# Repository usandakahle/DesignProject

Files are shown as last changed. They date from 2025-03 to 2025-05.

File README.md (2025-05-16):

# Micromouse Power Module System

This project is the power module circuit for the EEE3088F design project that provides power to the micromouse system

## Features

-  Boost Converter (3.7V → 5V @ 1.5A)
-  LDO Regulator (5V → 3.3V @ 300mA)
-  Dual H-Bridge Motor Driver (DRV8833 for 4x brushed DC motors)
-  High-Side Load Switches (TPS2HB50-Q1, 2 channels @ 1A each)
-  Physical ON/OFF switch with <30µA shutdown current
-  USB-C Female Connector
-  CH224K PD Negotiation (9V)
-  Linear Voltage Regulator, LM7805 (5V)
-  LiPo Battery Charging IC, TC4056A
-  Small PCB footprint, JLCPCB-ready
-  -All features and components are sourced from JLCPCB (https://jlcpcb.com/parts/all-electronic-components) 
  
---

##  Design Overview

- Input: 3.7V Li-ion (1S1P)
- USB-C Input: 9V
- Voltage Regulation:
  - Boost: MT3608
  - 3.3V Regulator: AMS1117-3.3 or TLV75533P
  - 5V Regulator: LM7805
- Motor Driver: DRV8833, controls 4 DC motors bidirectionally
- Load Switches:TPS2HB50-Q1 with configurable ILIM resistors
- ON/OFF Circuit: Slide switch + pMOS + NPN low-quiescent design

---

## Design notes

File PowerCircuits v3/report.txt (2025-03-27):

Error: Update symbols CN1 CN1 from 'batt_conn:B2B-PH-K-S(LF)(SN)' to 'batt_conn:B2B-PH-K-S(LF)(SN)': *** symbol not found ***
Error: Update symbols LED1 LED1 from 'led101:KT-0603R' to 'led101:KT-0603R': *** symbol not found ***
Error: Update symbols U6 U12 from 'npn:2N2222A' to 'npn:2N2222A': *** symbol not found ***
Error: Update symbols U5 U11 from 'tc4056:TC4056A' to 'tc4056:TC4056A': *** symbol not found ***
Update symbol TP4 from 'Connector:TestPoint' to 'Connector:TestPoint': OK
Update symbol TP3 from 'Connector:TestPoint' to 'Connector:TestPoint': OK
Update symbol TP5 from 'Connector:TestPoint' to 'Connector:TestPoint': OK
Update symbol TP7 from 'Connector:TestPoint' to 'Connector:TestPoint': OK
Update symbol TP6 from 'Connector:TestPoint' to 'Connector:TestPoint': OK
Update symbol C2 from 'Device:C_Small' to 'Device:C_Small': OK
Update symbol R6 from 'Device:R_Small_US' to 'Device:R_Small_US': OK
Update symbol R7 from 'Device:R_Small_US' to 'Device:R_Small_US': OK
Update symbol C10 from 'Device:C_Small' to 'Device:C_Small': OK
Update symbol C9 from 'Device:C_Small' to 'Device:C_Small': OK
Update symbol #PWR08 from 'power:GND' to 'power:GND': OK
Update symbol C1 from 'Device:C_Small' to 'Device:C_Small': OK
Update symbol U5 from 'Power_Management:TPS22929D' to 'Power_Management:TPS22929D': OK
Update symbol C3 from 'Device:C_Small' to 'Device:C_Small': OK
Update symbol C7 from 'Device:C_Small' to 'Device:C_Small': OK
Update symbol #PWR09 from 'power:GND' to 'power:GND': OK
Update symbols J1 J1 from 'Connector_Generic:Conn_02x16_Odd_Even' to 'Connector_Generic:Conn_02x16_Odd_Even': OK
Update symbol U3 from 'Regulator_Linear:AP2112K-3.3' to 'Regulator_Linear:AP2112K-3.3': OK
Update symbol U2 from 'Regulator_Switching:MT3608' to 'Regulator_Switching:MT3608': OK
Update symbol C5 from 'Device:C_Small' to 'Device:C_Small': OK
Update symbol C12 from 'Device:C_Small' to 'Device:C_Small': OK
Update symbol R4 from 'Device:R_Small_US' to 'Device:R_Small_US': OK
Update symbol R3 from 'Device:R_Small_US' to 'Device:R_Small_US': OK
Update symbol #PWR014 from 'power:GND' to 'power:GND': OK
Update symbol #PWR015 from 'power:GND' to 'power:GND': OK
Update symbol #PWR013 from 'power:GND' to 'power:GND': OK
Update symbol U6 from 'Driver_Motor:DRV8833PWP' to 'Driver_Motor:DRV8833PWP': OK
Update symbol C11 from 'Device:C_Small' to 'Device:C_Small': OK
Update symbol U4 from 'Power_Management:TPS22929D' to 'Power_Management:TPS22929D': OK
Update symbol C4 from 'Device:C_Small' to 'Device:C_Small': OK
Update symbol R1 from 'Device:R_Small_US' to 'Device:R_Small_US': OK
Update symbol R2 from 'Device:R_Small_US' to 'Device:R_Small_US': OK
Update symbol C6 from 'Device:C_Small' to 'Device:C_Small': OK
Update symbol #PWR010 from 'power:GND' to 'power:GND': OK
Update symbol Q1 from 'Transistor_FET:AO3401A' to 'Transistor_FET:AO3401A': OK
Update symbol #PWR07 from 'power:GND' to 'power:GND': OK
Update symbol #PWR017 from 'power:GND' to 'power:GND': OK
Update symbol #PWR06 from 'power:GND' to 'power:GND': OK
Update symbol #PWR05 from 'power:GND' to 'power:GND': OK
Update symbol #PWR018 from 'power:GND' to 'power:GND': OK
Update symbol #PWR023 from 'power:GND' to 'power:GND': OK
Update symbol D1 from 'Device:D_Schottky' to 'Device:D_Schottky': OK
Update symbol #PWR021 from 'power:GND' to 'power:GND': OK
Update symbol #PWR01 from 'power:GND' to 'power:GND': OK
Update symbol R5 from 'Device:R_Small_US' to 'Device:R_Small_US': OK
Update symbol U1 from 'Driver_Motor:DRV8833PWP' to 'Driver_Motor:DRV8833PWP': OK
Update symbol U7 from 'Slide Switch Korean Hroparts Elec:K3-1391B-51' to 'Slide Switch Korean Hroparts Elec:K3-1391B-51': OK
Update symbol #PWR024 from 'power:GND' to 'power:GND': OK
Update symbol #PWR016 from 'power:GND' to 'power:GND': OK
Update symbol #PWR02 from 'power:GND' to 'power:GND': OK
Update symbol C8 from 'Device:C_Small' to 'Device:C_Small': OK
Update symbol #PWR03 from 'power:GND' to 'power:GND': OK
Update symbol #PWR04 from 'power:GND' to 'power:GND': OK
Update symbol #PWR019 from 'power:GND' to 'power:GND': OK
Update symbols R6 R12 from 'Device:R_Small_US' to 'Device:R_Small_US': OK
Update symbols C1 C14 from 'Device:C_Small' to 'Device:C_Small': OK
Update symbols R5 R14 from 'Device:R_Small_US' to 'Device:R_Small_US': OK
Update symbols TP2 TP2 from 'Connector:TestPoint' to 'Connector:TestPoint': OK
Update symbols JP2 JP2 from 'Jumper:Jumper_2_Open' to 'Jumper:Jumper_2_Open': OK
Update symbols R2 R8 from 'Device:R_Small_US' to 'Device:R_Small_US': OK
Update symbols R1 R10 from 'Device:R_Small_US' to 'Device:R_Small_US': OK
Update symbols C2 C15 from 'Device:C_Small' to 'Device:C_Small': OK
Update symbols C3 C13 from 'Device:C_Small' to 'Device:C_Small': OK
Update symbols R10 R13 from 'Device:R_Small_US' to 'Device:R_Small_US': OK
Update symbols R4 R11 from 'Device:R_Small_US' to 'Device:R_Small_US': OK
Update symbols TP1 TP1 from 'Connector:TestPoint' to 'Connector:TestPoint': OK
Update symbols JP1 JP1 from 'Jumper:Jumper_2_Open' to 'Jumper:Jumper_2_Open': OK
Update symbols U2 U10 from 'Regulator_Linear:LM7805_TO220' to 'Regulator_Linear:LM7805_TO220': OK
Update symbols R3 R9 from 'Device:R_Small_US' to 'Device:R_Small_US': OK
Update symbol U8 from 'FUC-24F11-SNLB1:FUC-24F11-SNLB1' to 'FUC-24F11-SNLB1:FUC-24F11-SNLB1': OK
Update symbol U13 from 'INA219AIDCNR:INA219AIDCNR' to 'INA219AIDCNR:INA219AIDCNR': OK
Update symbol U9 from 'CH224K:CH224K' to 'CH224K:CH224K': OK

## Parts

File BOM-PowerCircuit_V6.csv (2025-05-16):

Comment | Designator | Footprint | LCSC | Quantity
1k | R10,R11,R14 | R_0402_1005Metric_Pad0.72x0.64mm_HandSolder | C11702 | 3
2.2 uF | C4,C8 | C_0402_1005Metric_Pad0.74x0.62mm_HandSolder | C12530 | 2
AO3401A | Q1 | SOT-23 | C15127 | 1
10nF | C6 | C_0402_1005Metric_Pad0.74x0.62mm_HandSolder | C15195 | 1
10nF | C11,C12,C14,C15,C5 | C_0402_1005Metric_Pad0.74x0.62mm_HandSolder | C15525 | 5
6.8k | R8 | R_0805_2012Metric_Pad1.20x1.40mm_HandSolder | C17772 | 1
1 | R4,R5,R6,R7 | R_1206_3216Metric_Pad1.30x1.75mm_HandSolder | C17928 | 4
KT-0603R | LED1 | LED0603-RD | C2286 | 1
75k | R1 | R_0603_1608Metric_Pad0.98x0.95mm_HandSolder | C23242 | 1
D_Schottky | D1 | D_SMA | C2480 | 1
10k | R2,R9 | R_0402_1005Metric_Pad0.72x0.64mm_HandSolder | C25744 | 2
47k | R3 | R_0402_1005Metric_Pad0.72x0.64mm_HandSolder | C25792 | 1
2k | R12 | R_0402_1005Metric_Pad0.72x0.64mm_HandSolder | C4109 | 1
TPS22929D | U4,U5 | SOT-23-6 | C415177 | 2
5.6k | R13 | R_0805_2012Metric_Pad1.20x1.40mm_HandSolder | C4382 | 1
DRV8833PWP | U1,U12 | TSSOP-16_L5.0-W4.4-P0.65-LS6.4-BL-EP | C50506 | 2
LM7805S/TR | U10 | TO-263-3_L8.6-W10.2-P2.54-LS14.4-BR | C507146 | 1
AP2112K-3.3 | U3 | SOT-23-5 | C51118 | 1
1uF | C1,C10,C13,C2,C3,C7,C9 | C_0402_1005Metric_Pad0.74x0.62mm_HandSolder | C52923 | 7
FUC-24F11-SNLB1 | U8 | USB-C-SMD_C67380 | C67380 | 1
TC4056A | U11 | ESOP-8_L4.9-W3.9-P1.27-LS6.0-BR-EP3.3 | C84051 | 1
MT3608 | U2 | SOT-23-6 | C84817 | 1
MMBT2222A_C8512 | U14 | SOT-23-3_L2.9-W1.3-P1.90-LS2.4-BR | C8512 | 1
INA219AIDCNR | U13 | SOT-23-8_L3.0-W1.7-P0.65-LS2.8-BR | C87469 | 1
K3-1391B-51 | U7 | SW-TH_K3-1391B-51 | C92656 | 1
CH224K | U9 | ESSOP-10_L4.9-W3.9-P1.0-LS6.0-TL-EP | C970725 | 1
External Load out | TP6 | TestPoint_Pad_1.0x1.0mm |  | 1
TestPoint | TP3 | TestPoint_Pad_1.0x1.0mm |  | 1
Jumper_2_Open | JP3 | SolderJumper-2_P1.3mm_Open_TrianglePad1.0x1.5mm |  | 1
TestPoint | TP2 | TestPoint_Pad_1.0x1.0mm |  | 1
3.3V out | TP5 | TestPoint_Pad_1.0x1.0mm |  | 1
Jumper_2_Open | JP1 | SolderJumper-2_P1.3mm_Open_TrianglePad1.0x1.5mm |  | 1
5V out | TP4 | TestPoint_Pad_1.0x1.0mm |  | 1
Jumper_2_Open | JP4 | SolderJumper-2_P1.3mm_Open_TrianglePad1.0x1.5mm |  | 1
Jumper_2_Open | JP2 | SolderJumper-2_P1.3mm_Open_TrianglePad1.0x1.5mm |  | 1
Ext load out | TP7 | TestPoint_Pad_1.0x1.0mm |  | 1
TestPoint | TP1 | TestPoint_Pad_1.0x1.0mm |  | 1

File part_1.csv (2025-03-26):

Source: | C:\Users\Bronwyn Biggs\OneDrive - University of Cape Town\UCT\THIRD Year\EEE3088F Design Principles\MM Project\part_1\part_1.kicad_sch
Date: | 2025/03/24 22:11:09
Tool: | Eeschema 7.0.1
Generator: | C:\Program Files\KiCad\7.0\bin\scripting\plugins/bom_csv_grouped_by_value_with_fp.py
Component Count: | 2
Ref | Qnty | Value | Cmp name | Footprint | Description | Vendor | DNP
J1 | 1 | Conn_02x16_Odd_Even | Conn_02x16_Odd_Even | Connector_PinHeader_2.54mm:PinHeader_2x16_P2.54mm_Vertical | Generic connector, double row, 02x16, odd/even pin numbering scheme (row 1 odd numbers, row 2 even numbers), script generated (kicad-library-utils/schlib/autogen/connector/)
U1 | 1 | INA219AxD | INA219AxD | Package_SO:SOIC-8_3.9x4.9mm_P1.27mm | Zero-Drift, Bidirectional Current/Power Monitor (0-26V) With I2C Interface, SOIC-8

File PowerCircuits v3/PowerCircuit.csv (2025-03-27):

Source: | C:\Users\Sandakahle\OneDrive - University of Cape Town\3rd Year\EEE3088F\Project\CAD\PowerCircuits\PowerCircuit.kicad_sch
Date: | 2025/03/27 11:51:07
Tool: | Eeschema 7.0.1
Generator: | C:\Program Files\KiCad\7.0\bin\scripting\plugins/bom_csv_grouped_by_value.py
Component Count: | 56
Collated Components:
Item | Qty | Reference(s) | Value | LibPart | Footprint | Datasheet | DNP | LCSC | Part #
1 | 5 | C1, C3, C7, C9, C10 | 1uF | Device:C_Small | Capacitor_SMD:C_1206_3216Metric_Pad1.33x1.80mm_HandSolder | ~ |  |  | C1848
2 | 1 | C2 | 1 uF | Device:C_Small | Capacitor_SMD:C_1206_3216Metric_Pad1.33x1.80mm_HandSolder | ~
3 | 2 | C4, C11 | 2.2 uF | Device:C_Small | Capacitor_SMD:C_0402_1005Metric_Pad0.74x0.62mm_HandSolder | ~ |  |  | C12530
4 | 2 | C5, C12 | 10 uF | Device:C_Small | Capacitor_SMD:C_1206_3216Metric_Pad1.33x1.80mm_HandSolder | ~
5 | 2 | C6, C8 | 0.01uF | Device:C_Small | Capacitor_SMD:C_0402_1005Metric_Pad0.74x0.62mm_HandSolder | ~ |  |  | C1524
6 | 1 | C13 | 1uF | Device:C_Small | Capacitor_SMD:C_0402_1005Metric_Pad0.74x0.62mm_HandSolder | ~
7 | 2 | C14, C15 | 10uf | Device:C_Small | Capacitor_SMD:C_0402_1005Metric_Pad0.74x0.62mm_HandSolder | ~
8 | 1 | CN1 | B2B-PH-K-S(LF)(SN) | batt_conn:B2B-PH-K-S(LF)(SN) | batt_conn:CONN-TH_B2B-PH-K-S | https://item.szlcsc.com/142630.html |  | C131337
9 | 1 | D1 | D_Schottky | Device:D_Schottky | Diode_SMD:D_SMA | ~ |  |  | C2480
10 | 1 | J1 | Conn_02x16_Odd_Even | Connector_Generic:Conn_02x16_Odd_Even | Connector_PinHeader_2.54mm:PinHeader_2x16_P2.54mm_Vertical | ~
11 | 2 | JP1, JP2 | Jumper_2_Open | Jumper:Jumper_2_Open | Jumper:SolderJumper-2_P1.3mm_Open_TrianglePad1.0x1.5mm | ~
12 | 1 | LED1 | KT-0603R | led101:KT-0603R | led101:LED0603-RD | https://item.szlcsc.com/347874.html |  | C2286
13 | 1 | Q1 | AO3401A | Transistor_FET:AO3401A | Package_TO_SOT_SMD:SOT-23 | http://www.aosmd.com/pdfs/datasheet/AO3401A.pdf
14 | 1 | R1 | 75k | Device:R_Small_US | Resistor_SMD:R_0603_1608Metric_Pad0.98x0.95mm_HandSolder | ~ |  |  | C23242
15 | 1 | R2 | 10k | Device:R_Small_US | Resistor_SMD:R_0805_2012Metric_Pad1.20x1.40mm_HandSolder | ~ |  |  | C17414
16 | 1 | R3 | 47k | Device:R_Small_US | Resistor_SMD:R_0805_2012Metric_Pad1.20x1.40mm_HandSolder | ~ |  |  | C17713
17 | 2 | R4, R5 | 1 | Device:R_Small_US | Resistor_SMD:R_0603_1608Metric_Pad0.98x0.95mm_HandSolder | ~ |  |  | C22936
18 | 2 | R6, R7 | 0.4 | Device:R_Small_US | Resistor_SMD:R_0603_1608Metric_Pad0.98x0.95mm_HandSolder | ~
19 | 1 | R8 | 6.8k | Device:R_Small_US | Resistor_SMD:R_0402_1005Metric_Pad0.72x0.64mm_HandSolder | ~
20 | 1 | R9 | 10k | Device:R_Small_US | Resistor_SMD:R_0402_1005Metric_Pad0.72x0.64mm_HandSolder | ~
21 | 3 | R10, R11, R14 | 1k | Device:R_Small_US | Resistor_SMD:R_0402_1005Metric_Pad0.72x0.64mm_HandSolder | ~
22 | 1 | R12 | 2k | Device:R_Small_US | Resistor_SMD:R_0402_1005Metric_Pad0.72x0.64mm_HandSolder | ~
23 | 1 | R13 | 6k | Device:R_Small_US | Resistor_SMD:R_0402_1005Metric_Pad0.72x0.64mm_HandSolder | ~
24 | 3 | TP1, TP2, TP3 | TestPoint | Connector:TestPoint | TestPoint:TestPoint_Pad_1.0x1.0mm | ~
25 | 1 | TP4 | 5V out | Connector:TestPoint | TestPoint:TestPoint_Pad_1.0x1.0mm | ~
26 | 1 | TP5 | 3.3V out | Connector:TestPoint | TestPoint:TestPoint_Pad_1.0x1.0mm | ~
27 | 1 | TP6 | External Load out | Connector:TestPoint | TestPoint:TestPoint_Pad_1.0x1.0mm | ~
28 | 1 | TP7 | Ext load out | Connector:TestPoint | TestPoint:TestPoint_Pad_1.0x1.0mm | ~
29 | 2 | U1, U6 | DRV8833PWP | Driver_Motor:DRV8833PWP | Package_SO:HTSSOP-16-1EP_4.4x5mm_P0.65mm_EP3.4x5mm_Mask2.46x2.31mm_ThermalVias | http://www.ti.com/lit/ds/symlink/drv8833.pdf
30 | 1 | U2 | MT3608 | Regulator_Switching:MT3608 | Package_TO_SOT_SMD:SOT-23-6 | https://www.olimex.com/Products/Breadboarding/BB-PWR-3608/resources/MT3608.pdf
31 | 1 | U3 | AP2112K-3.3 | Regulator_Linear:AP2112K-3.3 | Package_TO_SOT_SMD:SOT-23-5 | https://www.diodes.com/assets/Datasheets/AP2112.pdf
32 | 2 | U4, U5 | TPS22929D | Power_Management:TPS22929D | Package_TO_SOT_SMD:SOT-23-6 | http://www.ti.com/lit/ds/symlink/tps22929d.pdf
33 | 1 | U7 | K3-1391B-51 | Slide Switch Korean Hroparts Elec:K3-1391B-51 | footprint:SW-TH_K3-1391B-51 | https://item.szlcsc.com/93849.html?ref=editor&logined=true |  | C92656
34 | 1 | U8 | FUC-24F11-SNLB1 | FUC-24F11-SNLB1:FUC-24F11-SNLB1 | footprint:USB-C-SMD_C67380 | https://item.szlcsc.com/68475.html |  | C67380
35 | 1 | U9 | CH224K | CH224K:CH224K | footprint:ESSOP-10_L4.9-W3.9-P1.0-LS6.0-TL-EP | https://item.szlcsc.com/2976729.html |  | C970725
36 | 1 | U10 | LM7805_TO220 | Regulator_Linear:LM7805_TO220 | Package_TO_SOT_THT:TO-220-3_Vertical | https://www.onsemi.cn/PowerSolutions/document/MC7800-D.PDF
37 | 1 | U11 | TC4056A | tc4056:TC4056A | tc4056:ESSOP-10_L4.9-W3.9-P1.0-LS6.0-TL-EP | https://atta.szlcsc.com/upload/public/pdf/source/20220909/99A730BF861B4E3F85141583932B02D1.pdf |  | C84051
38 | 1 | U12 | 2N2222A | npn:2N2222A | npn:TO-92-3_L4.8-W3.7-P2.54-R | https://item.szlcsc.com/308449.html |  | C358533
39 | 1 | U13 | INA219AIDCNR | INA219AIDCNR:INA219AIDCNR | footprint:SOT-23-8_L3.0-W1.7-P0.65-LS2.8-BR | https://item.szlcsc.com/155588.html |  | C87469

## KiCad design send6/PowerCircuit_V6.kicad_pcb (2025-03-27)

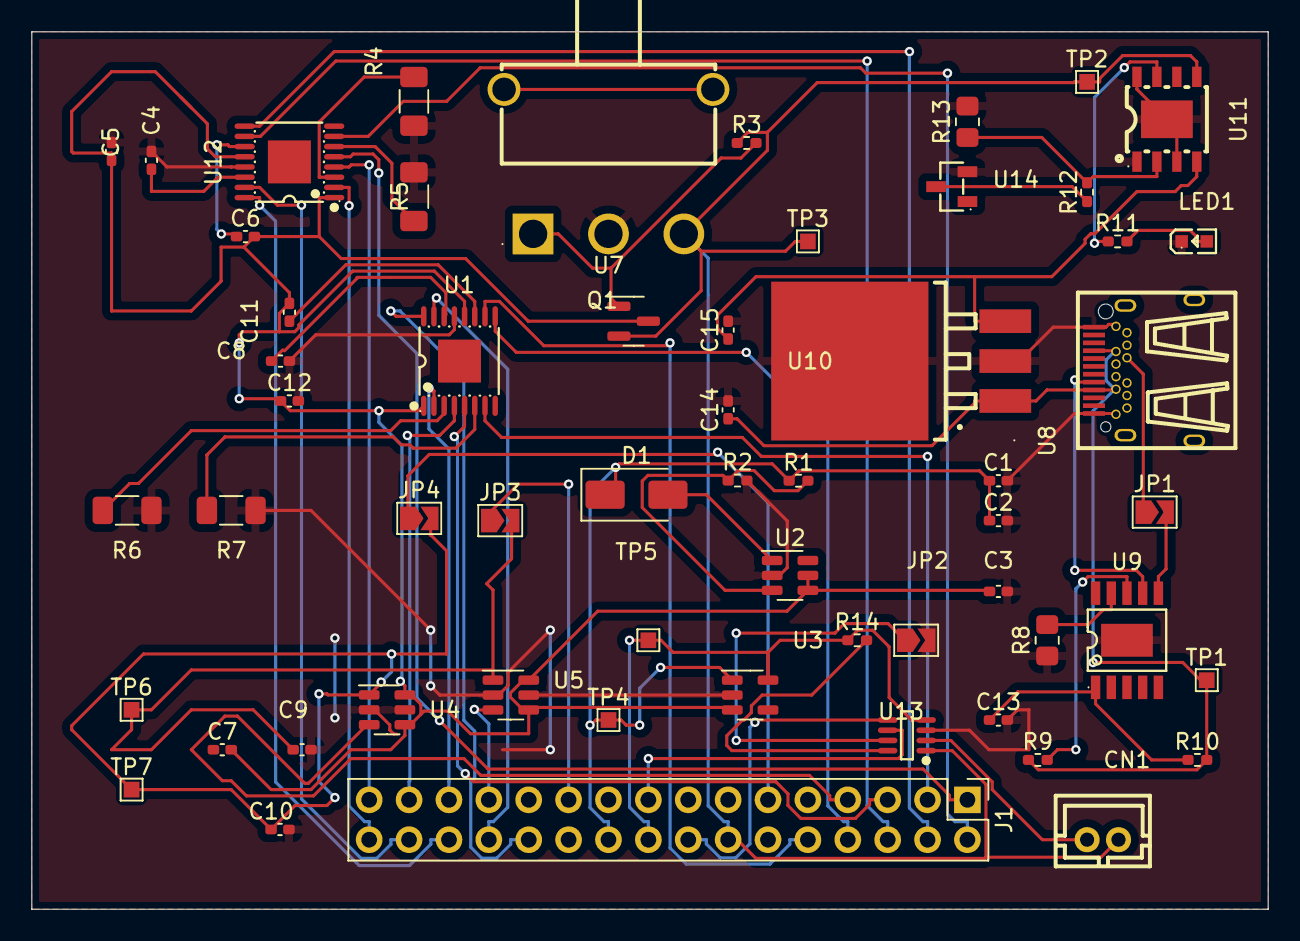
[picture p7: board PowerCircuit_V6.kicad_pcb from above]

Board: 2 copper layers, 78.7 x 55.9 mm, 58 parts (0 on the bottom side), 55 nets.

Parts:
C1, C2, C3, C7, C9, C10, C13: 1uF; C_0402_1005Metric_Pad0.74x0.62mm_HandSolder
C4, C8: 2.2 uF; C_0402_1005Metric_Pad0.74x0.62mm_HandSolder
C5, C12: 10 uF; C_0402_1005Metric_Pad0.74x0.62mm_HandSolder
C6, C11: 10nF; C_0402_1005Metric_Pad0.74x0.62mm_HandSolder
C14, C15: 10uF; C_0402_1005Metric_Pad0.74x0.62mm_HandSolder
CN1: B2B-PH-K-S(LF)(SN); CONN-TH_B2B-PH-K-S
D1: D_Schottky; D_SMA
J1: Conn_02x16_Odd_Even; PinHeader_2x16_P2.54mm_Vertical
JP1, JP2, JP3, JP4: Jumper_2_Open; SolderJumper-2_P1.3mm_Open_TrianglePad1.0x1.5mm
LED1: KT-0603R; LED0603-RD
Q1: AO3401A; SOT-23
R1: 75k; R_0402_1005Metric_Pad0.72x0.64mm_HandSolder
R2, R9: 10k; R_0402_1005Metric_Pad0.72x0.64mm_HandSolder
R3: 47k; R_0402_1005Metric_Pad0.72x0.64mm_HandSolder
R4, R5, R6, R7: 1; R_1206_3216Metric_Pad1.30x1.75mm_HandSolder
R8: 6.8k; R_0805_2012Metric_Pad1.20x1.40mm_HandSolder
R10, R11, R14: 1k; R_0402_1005Metric_Pad0.72x0.64mm_HandSolder
R12: 2k; R_0402_1005Metric_Pad0.72x0.64mm_HandSolder
R13: 5.6k; R_0805_2012Metric_Pad1.20x1.40mm_HandSolder
TP1, TP2, TP3: TestPoint; TestPoint_Pad_1.0x1.0mm
TP4: 5V out; TestPoint_Pad_1.0x1.0mm
TP5: 3.3V out; TestPoint_Pad_1.0x1.0mm
TP6: External Load out; TestPoint_Pad_1.0x1.0mm
TP7: Ext load out; TestPoint_Pad_1.0x1.0mm
U1, U12: DRV8833PWP; TSSOP-16_L5.0-W4.4-P0.65-LS6.4-BL-EP
U2: MT3608; SOT-23-6
U3: AP2112K-3.3; SOT-23-5
U4, U5: TPS22929D; SOT-23-6
U7: K3-1391B-51; SW-TH_K3-1391B-51
U8: FUC-24F11-SNLB1; USB-C-SMD_C67380
U9: CH224K; ESSOP-10_L4.9-W3.9-P1.0-LS6.0-TL-EP
U10: LM7805S/TR; TO-263-3_L8.6-W10.2-P2.54-LS14.4-BR
U11: TC4056A; ESOP-8_L4.9-W3.9-P1.27-LS6.0-BR-EP3.3
U13: INA219AIDCNR; SOT-23-8_L3.0-W1.7-P0.65-LS2.8-BR
U14: MMBT2222A_C8512; SOT-23-3_L2.9-W1.3-P1.90-LS2.4-BR

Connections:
/3V3: J1.18, R14.1, TP5.1, U3.5 (VOUT), U13.4 (VS)
/5V: C1.1, C2.1, D1.1 (K), J1.20, R1.1, TP4.1, U3.1 (VIN)
/BATTERY: CN1.1, J1.14, Q1.2 (S), R3.1, TP2.1, TP3.1, U7.3, U11.5 (BAT), U13.1 (IN+)
/BATT_OUT: CN1.2, U13.2 (IN-)
/CC1: U8.A5 (CC1), U9.7 (CC1)
/CC2: JP1.2 (B), U9.6 (CC2)
/CTRL_EXT_LOAD1: J1.25, U5.3 (ON)
/CTRL_EXT_LOAD2: J1.7, U4.3 (ON)
/EXT_LOAD1_OUT: J1.21, JP3.1 (A)
/EXT_LOAD2_OUT: J1.11, JP4.1 (A)
/I2C1_SCL: J1.16, U13.5 (SCL)
/I2C1_SDA: J1.17, U13.6 (SDA)
/MOTOR1_A_OUT: J1.32, U12.2 (AOUT1)
/MOTOR1_B_OUT: J1.31, U12.4 (AOUT2)
/MOTOR1_CTRL1: J1.28, U12.16 (AIN1)
/MOTOR1_CTRL2: J1.30, U12.15 (AIN2)
/MOTOR2_A_OUT: J1.2, U12.7 (BOUT1)
/MOTOR2_B_OUT: J1.1, U12.5 (BOUT2)
/MOTOR2_CTRL1: J1.4, U12.9 (BIN1)
/MOTOR2_CTRL2: J1.6, U12.10 (BIN2)
/MOTOR3_A_OUT: J1.27, U1.2 (AOUT1)
/MOTOR3_B_OUT: J1.29, U1.4 (AOUT2)
/MOTOR3_CTRL1: J1.24, U1.16 (AIN1)
/MOTOR3_CTRL2: J1.26, U1.15 (AIN2)
/MOTOR4_A_OUT: J1.3, U1.7 (BOUT1)
/MOTOR4_B_OUT: J1.5, U1.5 (BOUT2)
/MOTOR4_CTRL1: J1.8, U1.9 (BIN1)
/MOTOR4_CTRL2: J1.10, U1.10 (BIN2)
/PROG: R12.2, R13.1, U11.2 (PROG)
/PWR_OUT: C3.1, C5.1, C6.2, C7.2, C11.2, C12.1, Q1.3 (D), U1.1 (nSleep), U1.12 (VM), U2.4 (EN), U2.5 (IN), U3.3 (EN), U4.4 (VIN), U4.6 (VIN), U5.4 (VIN), U5.6 (VIN), U12.1 (nSleep), U12.12 (VM)
/Step_5V: C15.1, U10.3 (OUT), U11.4 (VCC)
/VBUS: C14.1, R9.1, R10.2, TP1.1, U8.A4 (VBUS), U8.A9 (VBUS), U8.B4 (VBUS), U8.B9 (VBUS), U10.1 (VCC)
GND: C1.2, C2.2, C3.2, C4.2, C5.2, C7.1, C8.2, C9.2, C10.2, C12.2, C13.2, C14.2, C15.2, J1.19, J1.23, JP2.2 (B), LED1.1 (K), R2.2, R4.1, R5.2, R6.1, R7.2, R8.1, R13.2, U1.13 (GND), U2.2 (GND), U3.2 (GND), U4.2 (GND), U4.5 (GND), U5.2 (GND), U5.5 (GND), U7.2, U8.A1 (GND), U8.A12 (GND), U8.B1 (GND), U8.B12 (GND), U9.11 (GND), U10.2 (GND), U10.4 (GND), U11.1 (TEMP), U11.3 (GND), U11.8 (CE), U11.9 (EP), U12.13 (GND), U13.3 (GND), U14.2 (E)
unnamed: D1.2 (A), U2.1 (SW)
unnamed: JP1.1 (A), U8.B5 (CC2)
unnamed: JP2.1 (A), U13.7 (A0)
unnamed: C9.1, JP3.2 (B), TP6.1, U5.1 (VOUT)
unnamed: C10.1, JP4.2 (B), TP7.1, U4.1 (VOUT)
unnamed: LED1.2 (A), R11.2
unnamed: Q1.1 (G), R3.2, U7.1
unnamed: R6.2, U1.3 (AISEN)
unnamed: R7.1, U1.6 (BISEN)
unnamed: C11.1, U1.11 (VCP)
unnamed: C8.1, U1.14 (VINT)
unnamed: R1.2, R2.1, U2.3 (FB)
unnamed: R8.2, U9.9 (CFG1)
unnamed: R9.2, U9.8 (VBUS)
unnamed: C13.1, R10.1, U9.1 (VDD)
unnamed: R11.1, U11.7 (CHRG)
unnamed: R4.2, U12.3 (AISEN)
unnamed: R5.1, U12.6 (BISEN)
unnamed: C6.1, U12.11 (VCP)
unnamed: C4.1, U12.14 (VINT)
unnamed: R14.2, U13.8 (A1)
unnamed: R12.1, U14.3 (C)

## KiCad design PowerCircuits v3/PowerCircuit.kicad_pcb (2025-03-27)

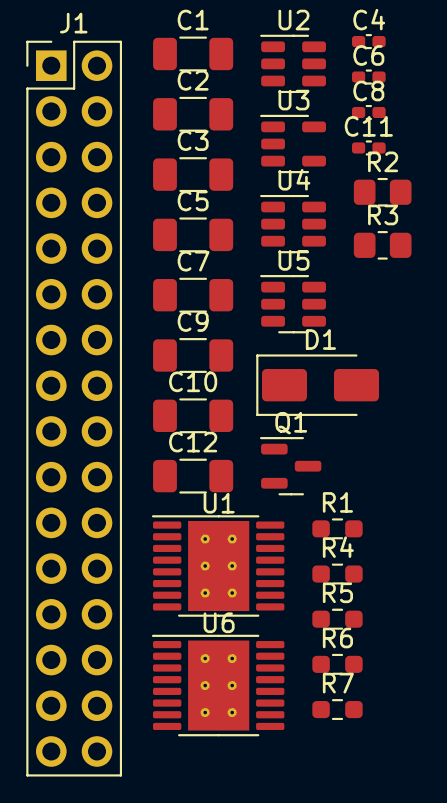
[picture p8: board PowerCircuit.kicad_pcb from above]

Board: 2 copper layers, 28 parts (0 on the bottom side), 36 nets, no tracks yet.

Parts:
C1, C3, C7, C9, C10: 1uF; C_1206_3216Metric_Pad1.33x1.80mm_HandSolder
C2: 1 uF; C_1206_3216Metric_Pad1.33x1.80mm_HandSolder
C4, C11: 2.2 uF; C_0402_1005Metric_Pad0.74x0.62mm_HandSolder
C5, C12: 10 uF; C_1206_3216Metric_Pad1.33x1.80mm_HandSolder
C6, C8: 0.01uF; C_0402_1005Metric_Pad0.74x0.62mm_HandSolder
D1: D_Schottky; D_SMA
J1: Conn_02x16_Odd_Even; PinHeader_2x16_P2.54mm_Vertical
Q1: AO3401A; SOT-23
R1: 75k; R_0603_1608Metric_Pad0.98x0.95mm_HandSolder
R2: 10k; R_0805_2012Metric_Pad1.20x1.40mm_HandSolder
R3: 47k; R_0805_2012Metric_Pad1.20x1.40mm_HandSolder
R4, R5: 1; R_0603_1608Metric_Pad0.98x0.95mm_HandSolder
R6, R7: 0.4; R_0603_1608Metric_Pad0.98x0.95mm_HandSolder
U1, U6: DRV8833PWP; HTSSOP-16-1EP_4.4x5mm_P0.65mm_EP3.4x5mm_Mask2.46x2.31mm_The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
U2: MT3608; SOT-23-6
U3: AP2112K-3.3; SOT-23-5
U4, U5: TPS22929D; SOT-23-6

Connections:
/3V3: J1.18, U3.5 (VOUT)
/5V: C1.1, C2.1, D1.1 (K), J1.20, R1.1, U3.1 (VIN)
/BATTERY: J1.14, Q1.2 (S), R3.1
/CTRL_EXT_LOAD1: J1.25, U5.3 (ON)
/CTRL_EXT_LOAD2: J1.7, U4.3 (ON)
/EXT_LOAD1_OUT: C9.1, J1.21, U5.1 (VOUT)
/EXT_LOAD2_OUT: C10.1, J1.11, U4.1 (VOUT)
/MOTOR1_A_OUT: J1.32, U1.2 (AOUT1)
/MOTOR1_B_OUT: J1.31, U1.4 (AOUT2)
/MOTOR1_CTRL1: J1.28, U1.16 (AIN1)
/MOTOR1_CTRL2: J1.30, U1.15 (AIN2)
/MOTOR2_A_OUT: J1.2, U1.7 (BOUT1)
/MOTOR2_B_OUT: J1.1, U1.5 (BOUT2)
/MOTOR2_CTRL1: J1.4, U1.9 (BIN1)
/MOTOR2_CTRL2: J1.6, U1.10 (BIN2)
/MOTOR3_A_OUT: J1.27, U6.2 (AOUT1)
/MOTOR3_B_OUT: J1.29, U6.4 (AOUT2)
/MOTOR3_CTRL1: J1.24, U6.16 (AIN1)
/MOTOR3_CTRL2: J1.26, U6.15 (AIN2)
/MOTOR4_A_OUT: J1.3, U6.7 (BOUT1)
/MOTOR4_B_OUT: J1.5, U6.5 (BOUT2)
/MOTOR4_CTRL1: J1.8, U6.9 (BIN1)
/MOTOR4_CTRL2: J1.10, U6.10 (BIN2)
/PWR_OUT: C3.1, C5.1, C6.2, C7.2, C8.2, C12.1, Q1.3 (D), U1.1 (nSLEEP), U1.12 (VM), U2.4 (EN), U2.5 (IN), U3.3 (EN), U4.4 (VIN), U4.6 (VIN), U5.4 (VIN), U5.6 (VIN), U6.1 (nSLEEP), U6.12 (VM)
GND: C1.2, C2.2, C3.2, C4.2, C5.2, C7.1, C9.2, C10.2, C11.2, C12.2, J1.19, J1.23, R2.2, R4.1, R5.2, R6.2, R7.1, U1.13 (GND), U1.17 (GND(PPAD)), U2.2 (GND), U3.2 (GND), U4.2 (GND), U4.5 (GND), U5.2 (GND), U5.5 (GND), U6.13 (GND), U6.17 (GND(PPAD))
unnamed: D1.2 (A), U2.1 (SW)
unnamed: Q1.1 (G), R3.2
unnamed: R4.2, U1.3 (AISEN)
unnamed: R5.1, U1.6 (BISEN)
unnamed: C6.1, U1.11 (VCP)
unnamed: C4.1, U1.14 (VINT)
unnamed: R1.2, R2.1, U2.3 (FB)
unnamed: R6.1, U6.3 (AISEN)
unnamed: R7.2, U6.6 (BISEN)
unnamed: C8.1, U6.11 (VCP)
unnamed: C11.1, U6.14 (VINT)

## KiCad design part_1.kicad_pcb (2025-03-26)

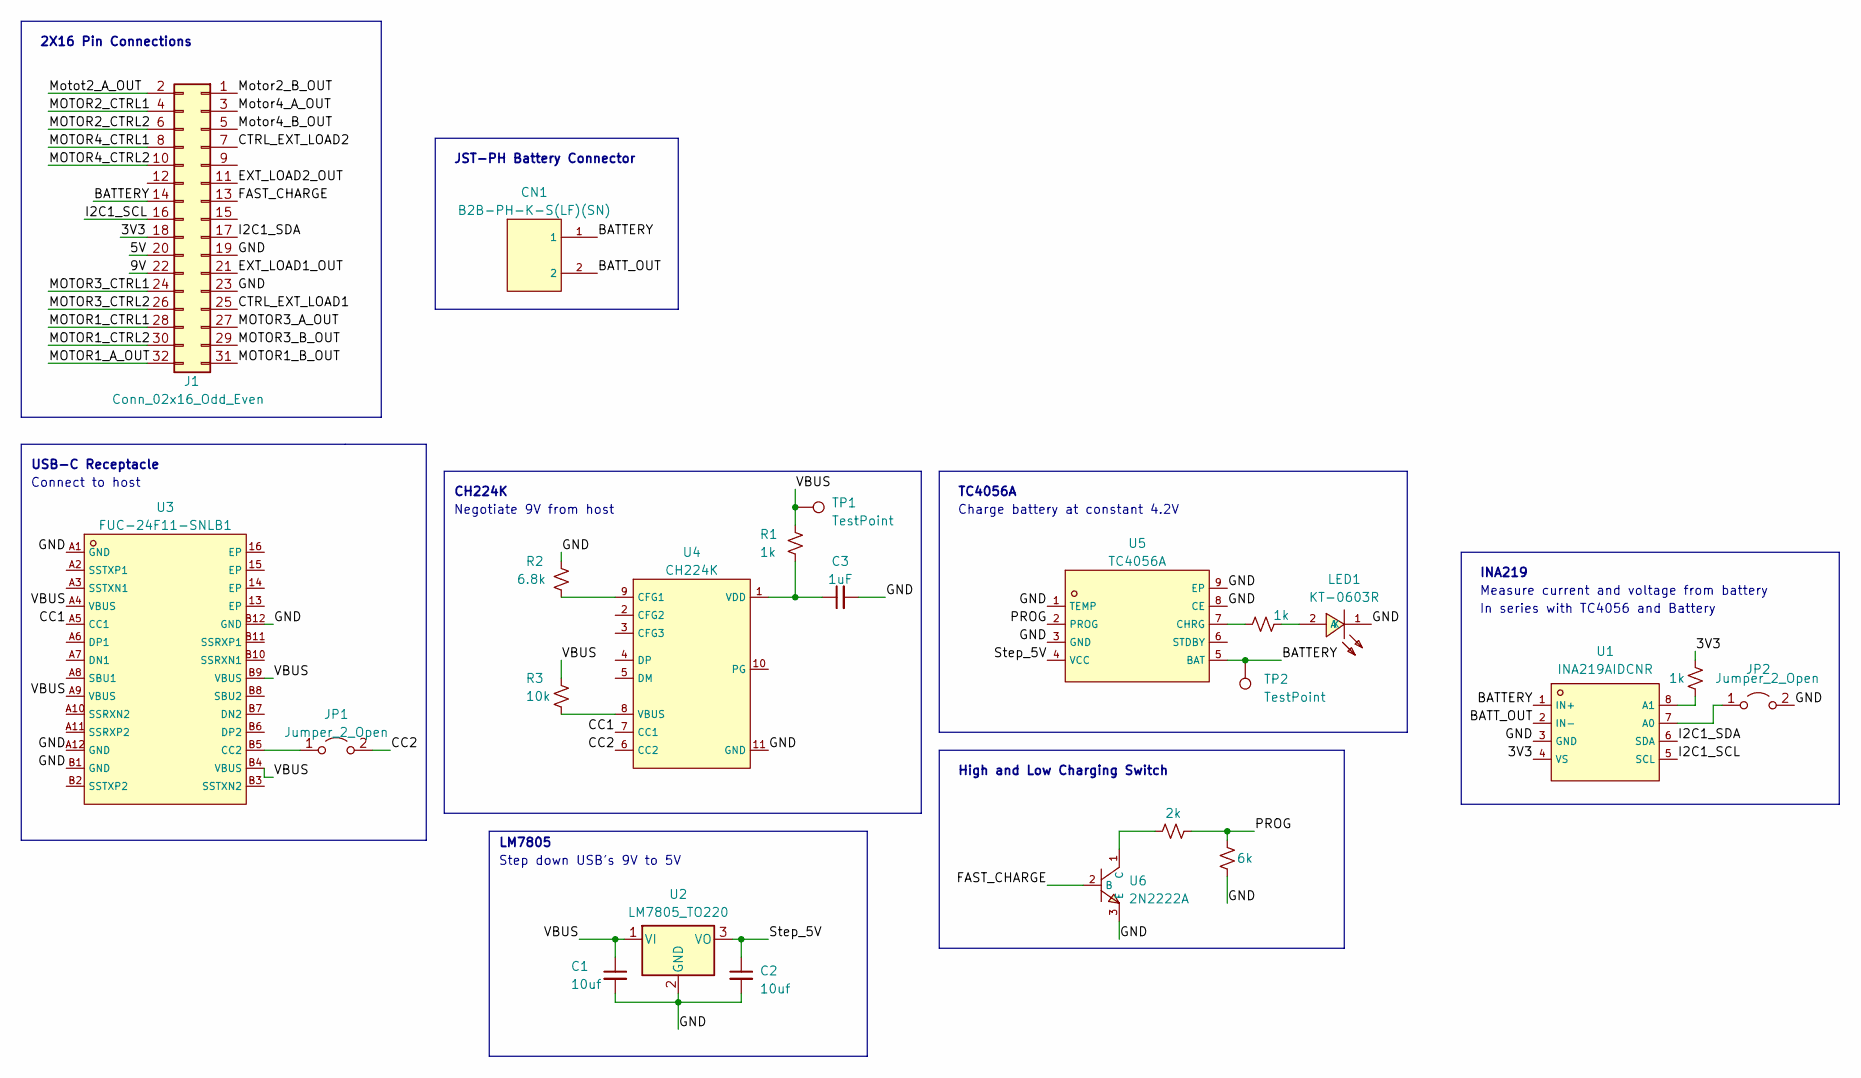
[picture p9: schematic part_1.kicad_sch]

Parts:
C1, C2: 10uf; C_0402_1005Metric_Pad0.74x0.62mm_HandSolder
C3: 1uF; C_0402_1005Metric_Pad0.74x0.62mm_HandSolder
CN1: B2B-PH-K-S(LF)(SN); CONN-TH_B2B-PH-K-S; LCSC C131337
J1: Conn_02x16_Odd_Even; PinHeader_2x16_P2.54mm_Vertical
JP1, JP2: Jumper_2_Open; SolderJumper-2_P1.3mm_Open_TrianglePad1.0x1.5mm
LED1: KT-0603R; LED0603-RD; LCSC C2286
R1, R4, R5: 1k; R_0402_1005Metric_Pad0.72x0.64mm_HandSolder
R2: 6.8k; R_0402_1005Metric_Pad0.72x0.64mm_HandSolder
R3: 10k; R_0402_1005Metric_Pad0.72x0.64mm_HandSolder
R6: 2k; R_0402_1005Metric_Pad0.72x0.64mm_HandSolder
R10: 6k; R_0402_1005Metric_Pad0.72x0.64mm_HandSolder
TP1, TP2: TestPoint; TestPoint_Pad_1.0x1.0mm
U1: INA219AIDCNR; SOT-23-8_L3.0-W1.7-P0.65-LS2.8-BR; LCSC C87469
U2: LM7805_TO220; TO-220-3_Vertical
U3: FUC-24F11-SNLB1; USB-C-SMD_C67380; Part # C67380
U4: CH224K; ESSOP-10_L4.9-W3.9-P1.0-LS6.0-TL-EP; Part # C970725
U5: TC4056A; ESSOP-10_L4.9-W3.9-P1.0-LS6.0-TL-EP; LCSC C84051
U6: 2N2222A; TO-92-3_L4.8-W3.7-P2.54-R; LCSC C358533

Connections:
/3V3: J1.18, R5.1, U1.4 (VS)
/5V: J1.20
/9V: J1.22
/BATTERY: CN1.1, J1.14, TP2.1, U1.1 (IN+), U5.5 (BAT)
/BATT_OUT: CN1.2, U1.2 (IN-)
/CC1: U3.A5 (CC1), U4.7 (CC1)
/CC2: JP1.2 (B), U4.6 (CC2)
/CTRL_EXT_LOAD1: J1.25
/CTRL_EXT_LOAD2: J1.7
/EXT_LOAD1_OUT: J1.21
/EXT_LOAD2_OUT: J1.11
/FAST_CHARGE: J1.13, U6.2 (B)
/GND: C1.2, C2.2, C3.2, J1.19, J1.23, JP2.2 (B), LED1.1 (K), R2.1, R10.2, U1.3 (GND), U2.2 (GND), U3.A1 (GND), U3.A12 (GND), U3.B1 (GND), U3.B12 (GND), U4.11 (GND), U5.1 (TEMP), U5.3 (GND), U5.8 (CE), U5.9 (EP), U6.3 (E)
/I2C1_SCL: J1.16, U1.5 (SCL)
/I2C1_SDA: J1.17, U1.6 (SDA)
/MOTOR1_A_OUT: J1.32
/MOTOR1_B_OUT: J1.31
/MOTOR1_CTRL1: J1.28
/MOTOR1_CTRL2: J1.30
/MOTOR2_CTRL1: J1.4
/MOTOR2_CTRL2: J1.6
/MOTOR3_A_OUT: J1.27
/MOTOR3_B_OUT: J1.29
/MOTOR3_CTRL1: J1.24
/MOTOR3_CTRL2: J1.26
/MOTOR4_CTRL1: J1.8
/MOTOR4_CTRL2: J1.10
/Motor2_B_OUT: J1.1
/Motor4_A_OUT: J1.3
/Motor4_B_OUT: J1.5
/Motot2_A_OUT: J1.2
/PROG: R6.2, R10.1, U5.2 (PROG)
/Step_5V: C2.1, U2.3 (VO), U5.4 (VCC)
/VBUS: C1.1, R1.2, R3.1, TP1.1, U2.1 (VI), U3.A4 (VBUS), U3.A9 (VBUS), U3.B4 (VBUS), U3.B9 (VBUS)
unnamed: JP1.1 (A), U3.B5 (CC2)
unnamed: JP2.1 (A), U1.7 (A0)
unnamed: LED1.2 (A), R4.2
unnamed: R5.2, U1.8 (A1)
unnamed: R2.2, U4.9 (CFG1)
unnamed: R3.2, U4.8 (VBUS)
unnamed: C3.1, R1.1, U4.1 (VDD)
unnamed: R4.1, U5.7 (CHRG)
unnamed: R6.1, U6.1 (C)

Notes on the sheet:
High and Low Charging Switch
2X16 Pin Connections
Measure current and voltage from battery
Charge battery at constant 4.2V
TC4056A
Step down USB's 9V to 5V
LM7805
Connect to host
In series with TC4056 and Battery
INA219
Negotiate 9V from host
CH224K
JST-PH Battery Connector
USB-C Receptacle

Board: 2 copper layers, 23 parts (0 on the bottom side), 21 nets, no tracks yet.

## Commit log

2025-03-26 git repo made for the project
    [PowerCircuit.csv, PowerCircuit.kicad_pcb, PowerCircuit.kicad_sch]
2025-03-26 Adding files despite line-ending warnings
    [PowerCircuit.csv, PowerCircuit.kicad_pcb, PowerCircuit.kicad_sch]
2025-03-27 Final Sanda parts schematic
    [PowerCircuit.kicad_pcb, PowerCircuit.kicad_sch]
2025-03-27 Version 3
    [PowerCircuit.csv, PowerCircuit.kicad_pcb, PowerCircuit.kicad_sch]
2025-04-23 Final Design (3D,pcb)
2025-05-16 BOM and CPL Files from JLCPCB Tools
    [BOM-PowerCircuit_V6.csv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]
